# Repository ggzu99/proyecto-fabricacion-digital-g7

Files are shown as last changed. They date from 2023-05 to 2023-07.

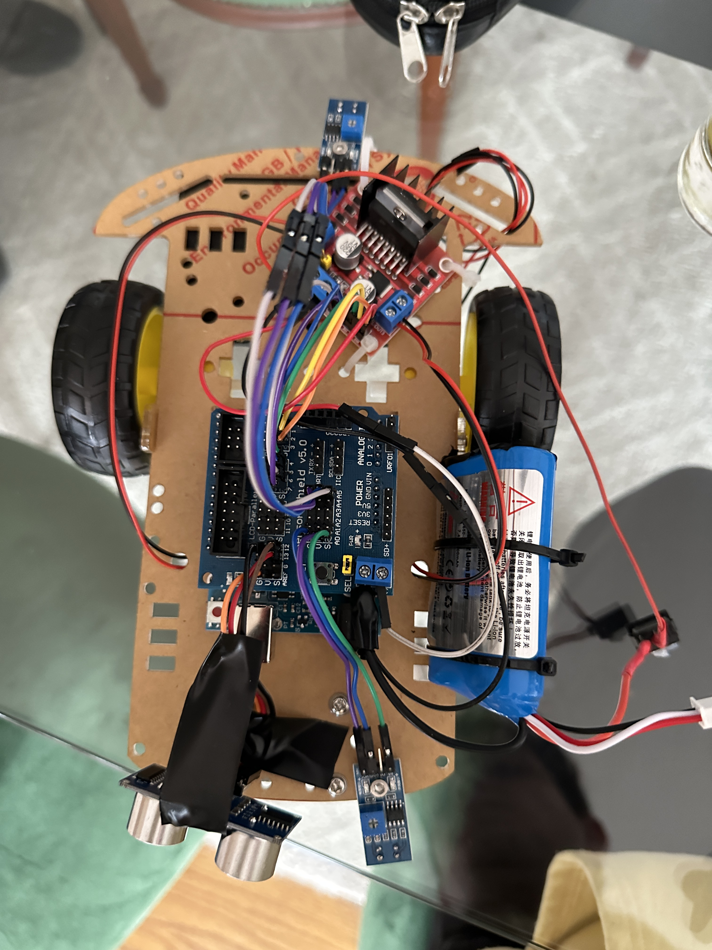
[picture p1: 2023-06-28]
Semana de Receso/MONTAJE_DE_PRUEBA_1.JPG

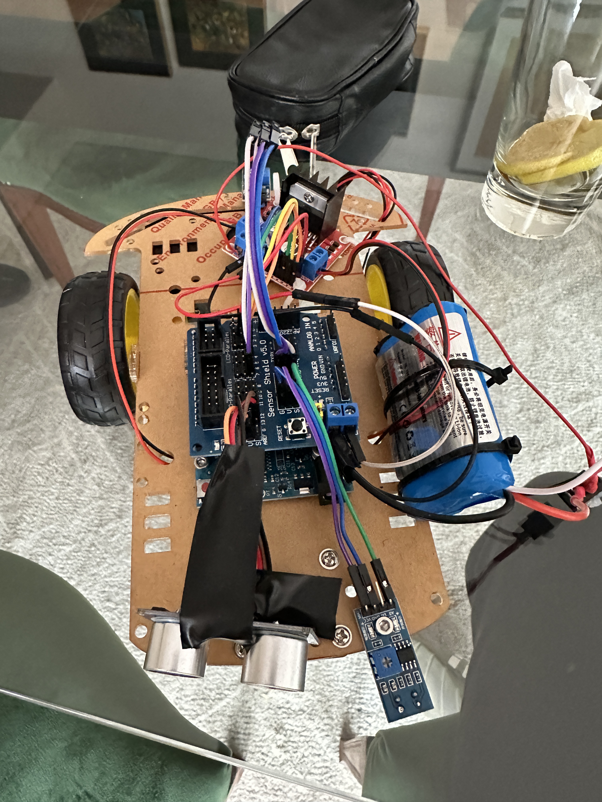
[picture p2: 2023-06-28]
Semana de Receso/MONTAJE_DE_PRUEBA_2.JPG

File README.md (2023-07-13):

# Proyecto "Robot Sumo" Grupo 7 + 6

En el presente repositorio se documentará el trabajo realizado para el proyecto semestral  
del ramo Fabricación Digital del departamento de ingeniería civil mecánica de la Universidad  
de Chile. 

Los avances semanales se encuentran ordenados por carpetas de nombre "Semana XX" donde XX corresponde a la  
semana de avance en cuestión. Los archivos actualizados y finales se encuentran en la carpeta "SEMANA 15". 

En la carpeta actualizada hay subcarpetas denominadas:
* **CAD**: Contiene todos los archivos CAD del proyecto, en formato universal .STP y un archivo PDF demostrativo de los componentes
  del robot.
* **MANUFACTURA**: Contiene el código g para manufacturar la parte inferior del chasis en Router CNC. Sumado a lo anterior tiene un
  documento llamado "Consideraciones Manufactura en CNC - Chasis Inferior" que entrega algunas consideraciones y recomendaciones
  para manufacturar el chasis.
* **STL**: Contiene los archivos .STL para poder procesar en software de impresión 3D e imprimir la cubierta de chasis, los soportes
  de sensores infrarojos, los soportes de motor y el portabatería.
* **SUMOCODE_FINAL**: Posee el archivo .ino correspondiente al código para cargar en el Arduino y que el robot funcione

Además, hay archivos adicionales, como "BOM FINAL" correspondiente a la lista de componentes y partes usadas y "Esquemático Sumobot",
el cual corresponde al esquemático electrónico del robot"

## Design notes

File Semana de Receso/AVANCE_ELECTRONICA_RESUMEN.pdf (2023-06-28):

1

Avances semana de receso - Electrónica

Para probar y hacer funcionar la electrónica de manera simple y rápida; con el fin de empezar a iterar el código y ojalá llegar a implementar una estrategia de batalla para el robot, se decidió comprar un kit robot de Arduino sigue líneas. Este incluía (en cuanto a electrónica):

- Arduino UNO
- Sensor Shield V5.0
- Controlador de Motores L298N
- 2 motores DC 3-6 V con reducción
- Sensor Ultrasónico HC-SR04

Sumado a los anteriores, se compraron dos (2) sensores infrarrojos TCRT-5000

Una vez adquiridos los componentes, se conectaron mediante el siguiente esquema, con algunas diferencias¹
:

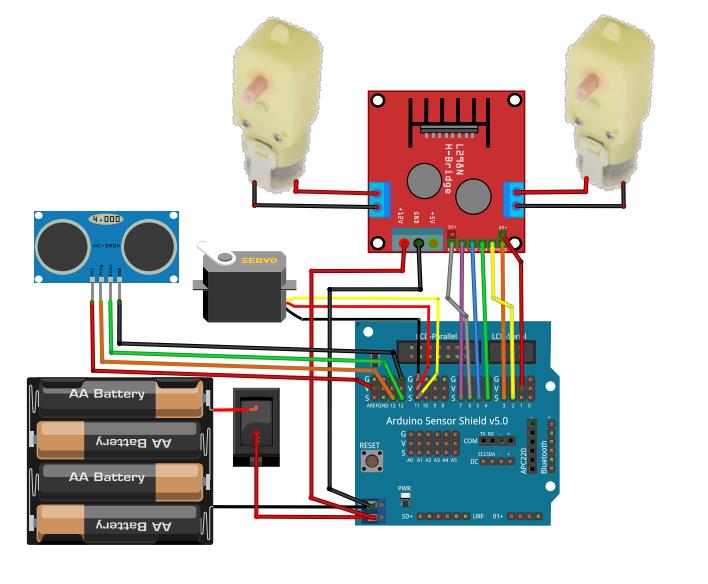
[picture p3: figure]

1
Se conectó la batería directamente al modulo controlador de motores L298N, de esa forma se aprovechó el regulador que trae, el cual al mantener el jumper activo (Fig 2.) permite tener una salida de 5V en VSS (Fig. 2), que sirve para suministrar corriente al Arduino y a la placa de sensores. Además no se utilizará el servomotor.

Figura 1. Esquemático.

2

Las conexiones realizadas fueron:

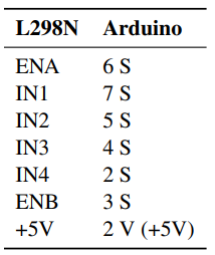
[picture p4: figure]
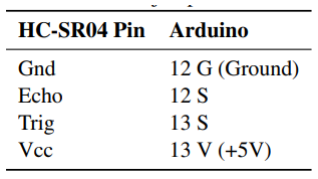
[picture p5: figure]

Como fuente de poder se está utilizando una batería LiPo de 7,4 V y 1800 mAh.

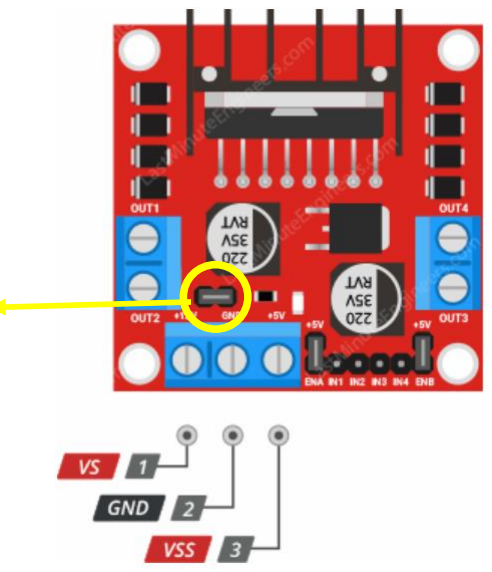
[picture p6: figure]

Figura 2. Power inputs and output L298N

JUMPER REGULADOR

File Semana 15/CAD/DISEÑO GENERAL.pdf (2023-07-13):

# Diseño General

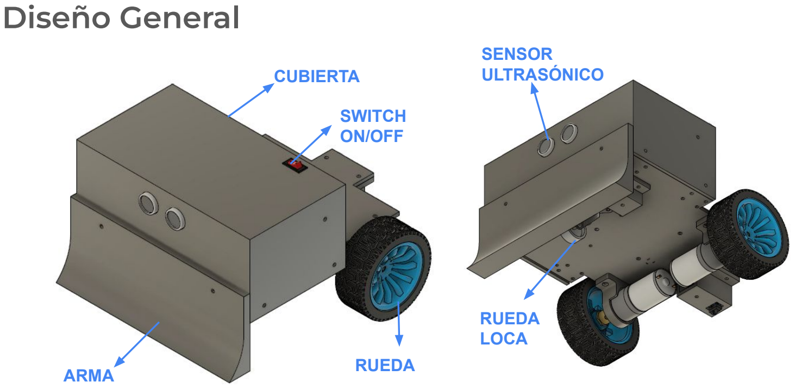
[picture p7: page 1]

ARMA

CUBIERTA

RUEDA

SWITCH
ON/OFF

SENSOR
ULTRASÓNICO

RUEDA
LOCA

# Diseño General

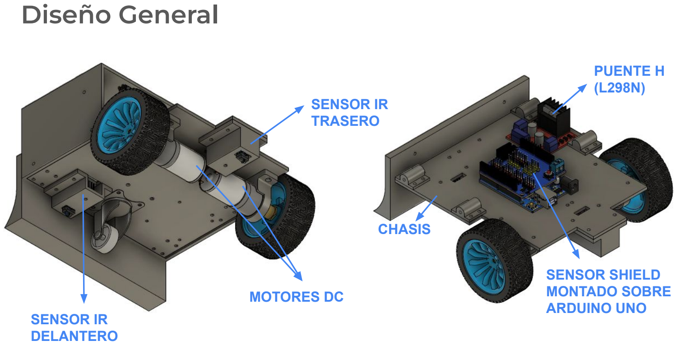
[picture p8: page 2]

MOTORES DC

SENSOR IR
TRASERO

SENSOR IR
DELANTERO

PUENTE H
(L298N)

SENSOR SHIELD
MONTADO SOBRE
ARDUINO UNO

CHASIS

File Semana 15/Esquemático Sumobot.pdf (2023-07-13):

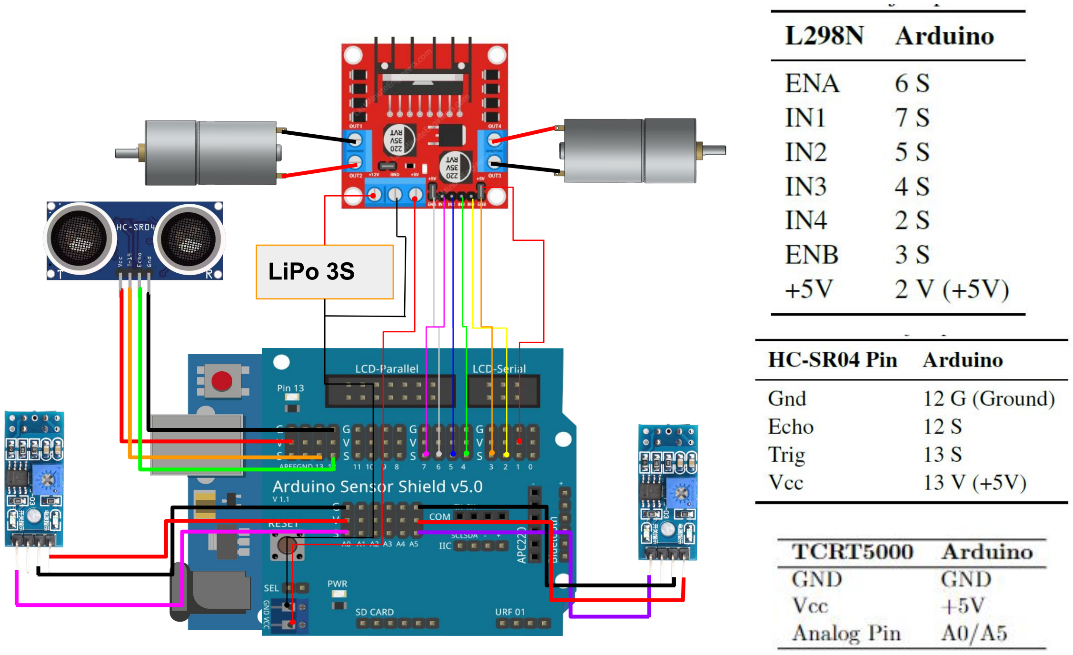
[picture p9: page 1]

LiPo 3S

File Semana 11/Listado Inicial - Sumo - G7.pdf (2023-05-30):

Curso: Fabricación Digital - ME4705-1 Diseño Conceptual

Listado inicial para desarrollo de Robot Sumo

1. Electrónica:
1.1. Arduino (ignacio)
1.2. Controlador de motores (ignacio)
1.3. Sensor Infrarrojo (Línea) (fablab)
1.4. Sensor Ultrasonico (Oponente) (fablab)
1.5. Motores (fablab)
1.6. Fuente de poder (fablab)
1.7. Switch encendido (fablab)
2. Mecánico:
2.1. Base (carton espuma - comprar)
2.2. Ruedas (fablab)
2.3. Arma (prototipo de carton)
3. Requerimientos de diseño:
3.1. 20 x 20 x 20 cm
3.2. <= 1000 g
3.3. No obstruir sensores del oponente

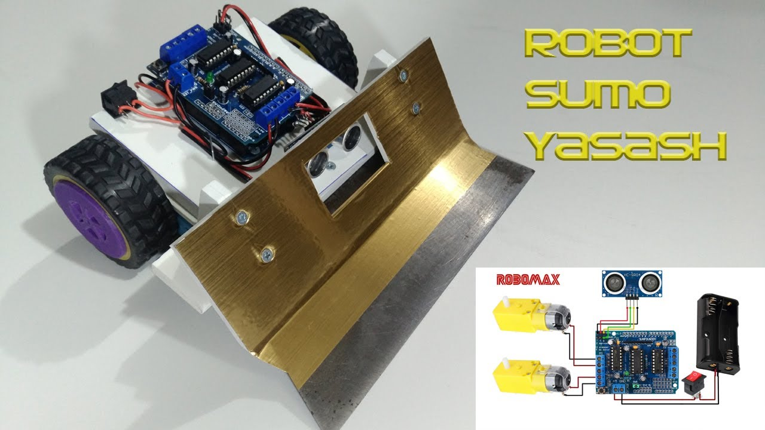
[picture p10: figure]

Links de interés:

- https://www.jsumo.com/sumo-robot-parts
- https://github.com/ggzu99/proyecto-fabricacion-digital-g7 ●

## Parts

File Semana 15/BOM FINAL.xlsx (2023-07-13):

BOM PARTES COMERCIALES SUMOBOT
Parte | Descripción | Cantidad | Tiendas (Chile)
Arduino UNO | Placa ARDUINO UNO R3 | 1 | AFEL (https://afel.cl/)
Sensor Shield | Placa para conectar sensores "Sensor Shield v5.0" que se monta sobre el Arduino | 1 | AFEL (https://afel.cl/)
LiPo 3S | Batería Lipo de 3 celdas, 11.1 V | 1 | REPUESTOSDRONE (https://repuestosdrone.cl/products/bateria-lipo-11-1v-1500-mah-35c-xt60?variant=35717458231447&currency=CLP)
Sensor Ultrasónico HC-SR04 | Sensor Ultrasónico para detectar enemigos | 1 | AFEL (https://afel.cl/)
Controlador de motor L298N | Controlador de motores que facilita la conexión a los mismos | 1 | AFEL (https://afel.cl/)
Sensor Infrarojo TCRT5000 | Sensor infrarojo para detectar línea blanca | 2 | AFEL (https://afel.cl/)
Ruedas 65 mm | Rueda traseras del robot de 65 mm de diámetro | 2 | RAMBAL (https://rambal.com/)
Rueda loca | Rueda delantera "Loca" | 1 | AFEL (https://afel.cl/)
Motor DC 12V | Motor DC 12V Modelo JGA25 100 RPM | 2 | RAMBAL (https://rambal.com/)
Acoplamiento Ruedas | Acoplamiento para ruedas Hexagonal 30x4 mm | 2 | RAMBAL (https://rambal.com/)
PERNERÍA
Tipo de Perno | Dimensiones | Cantidad | Tienda
ALLEN/PARKER | M3x10 mm | 32 | PERNOS KIM
ALLEN/PARKER | M3x8 mm | 4 | PERNOS KIM
ALLEN/PARKER | M3x20mm | 10 | PERNOS KIM

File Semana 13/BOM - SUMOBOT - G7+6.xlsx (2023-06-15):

Nombre de componente | Qty | Unit Cost | Total
Kit Arduino DIY Robot: | 1 | $36990 | $36990
Arduino UNO R3 | 1
Cable USB | 1
Shield expansión V5.0
Controlador de motor L298N | 1
Sensor Ultrasónico HC-SR04 | 1
Servomotor SG90 | 1
Placa fija de servomotor | 1
Motor DC | 2
Ruedas | 2
Rueda Libre | 1
Encoder 20 PPR | 2
Portapilas 4 x AA | 1
Placa acrílica chasis | 1
Sensor infrarojo TCRT5000 | 2 | $2300 | $4600
TOTAL |  |  | $41590

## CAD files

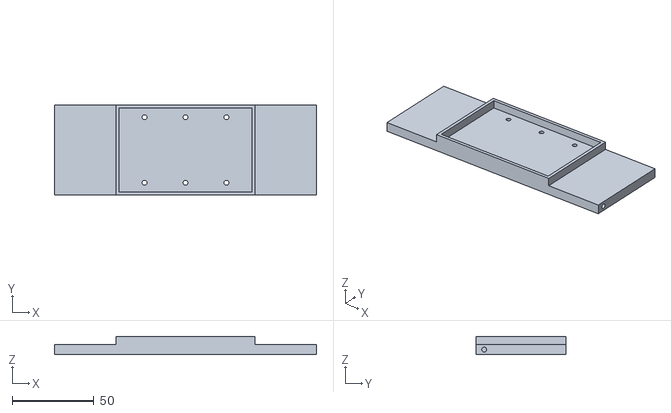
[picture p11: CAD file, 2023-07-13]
Semana 15/STL/portabatería.stl
160.0 x 55.0 x 11.0

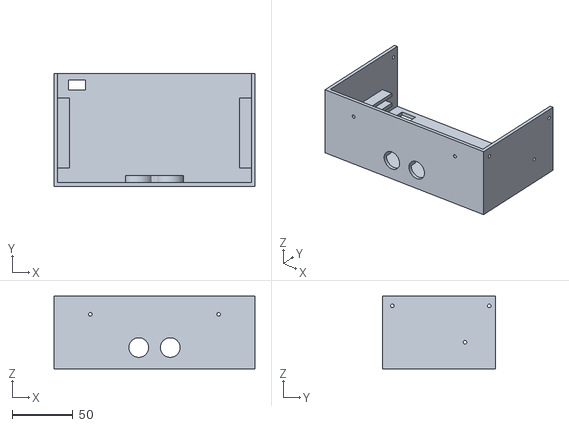
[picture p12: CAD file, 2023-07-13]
Semana 15/STL/cubierta.stl
166.0 x 93.0 x 60.0

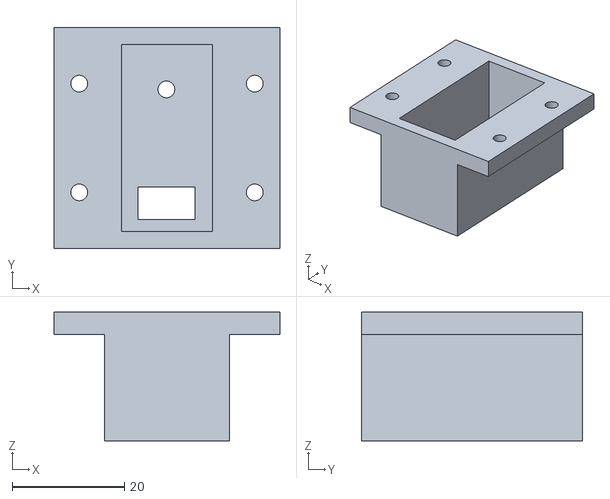
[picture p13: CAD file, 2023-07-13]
Semana 15/STL/soporte_IR_Trasero.stl
40.3 x 39.4 x 23.0

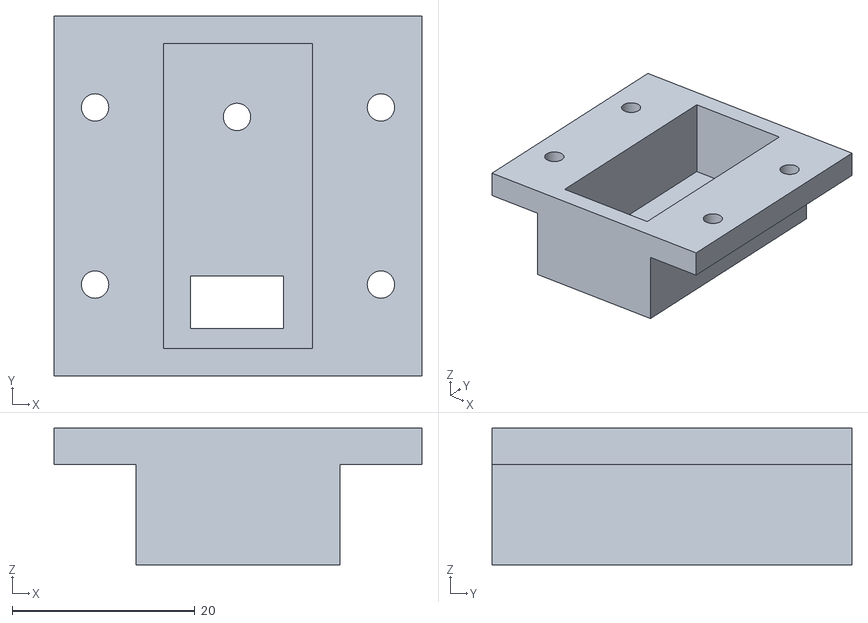
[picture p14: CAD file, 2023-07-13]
Semana 15/STL/soporte_IR_delantero.stl
40.3 x 39.4 x 15.0

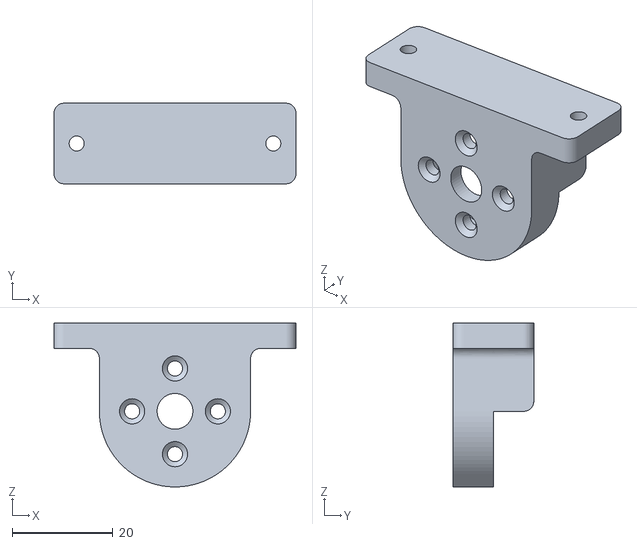
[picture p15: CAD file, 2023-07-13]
Semana 15/STL/motor_mount.stl
48.0 x 16.0 x 32.5

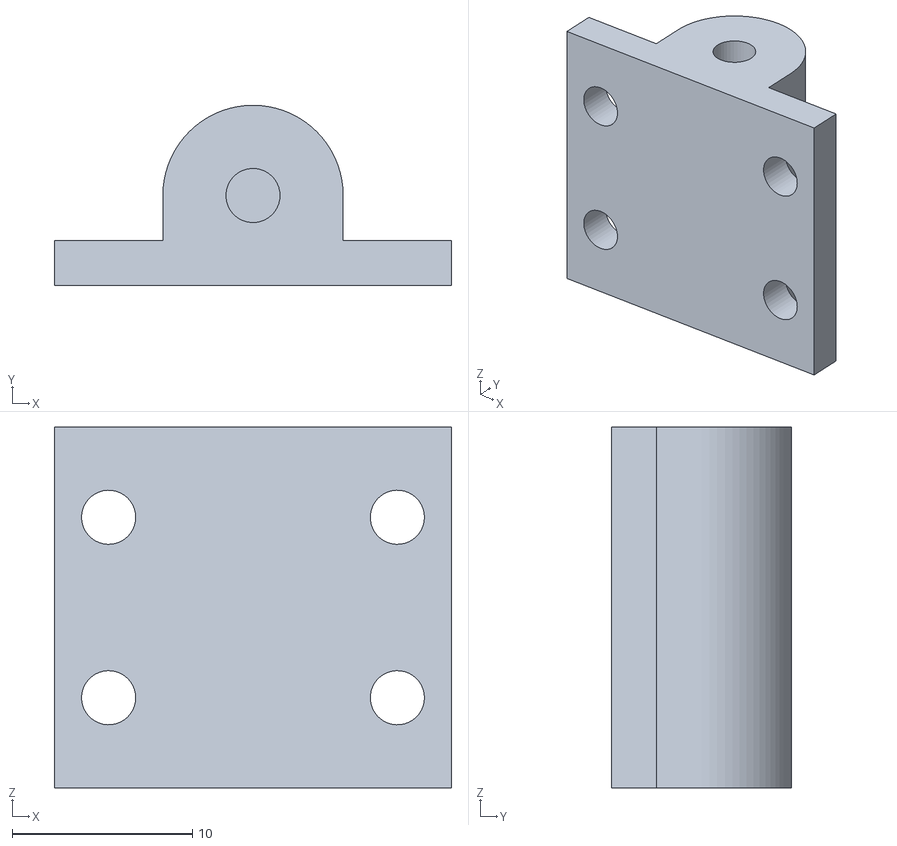
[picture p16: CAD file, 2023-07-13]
Semana 15/STL/fijaciones chasis-cubierta.stl
22.0 x 10.0 x 20.0

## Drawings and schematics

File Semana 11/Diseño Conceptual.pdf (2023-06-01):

# Sheman -

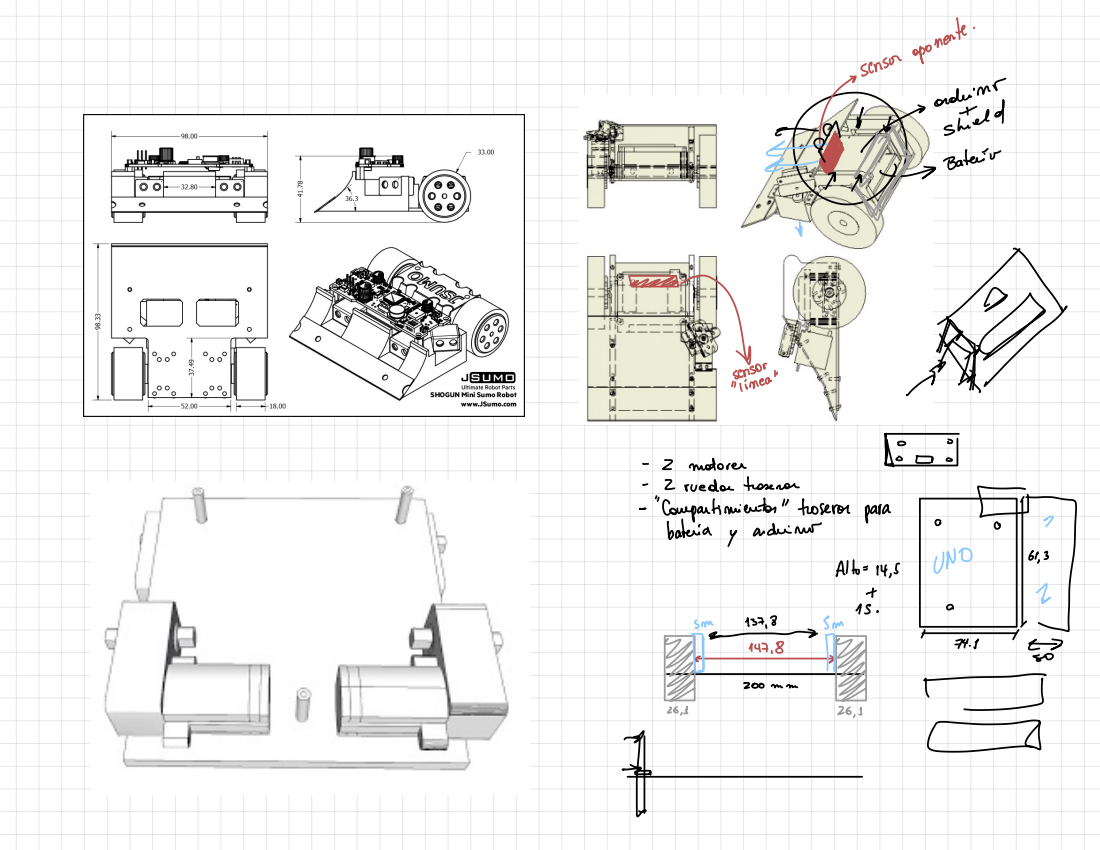
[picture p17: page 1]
sor; "limea"; motoren; rueden; tran; "Compartimiento"troseros; para; bateria; adeinu; Alto=14,; UNO

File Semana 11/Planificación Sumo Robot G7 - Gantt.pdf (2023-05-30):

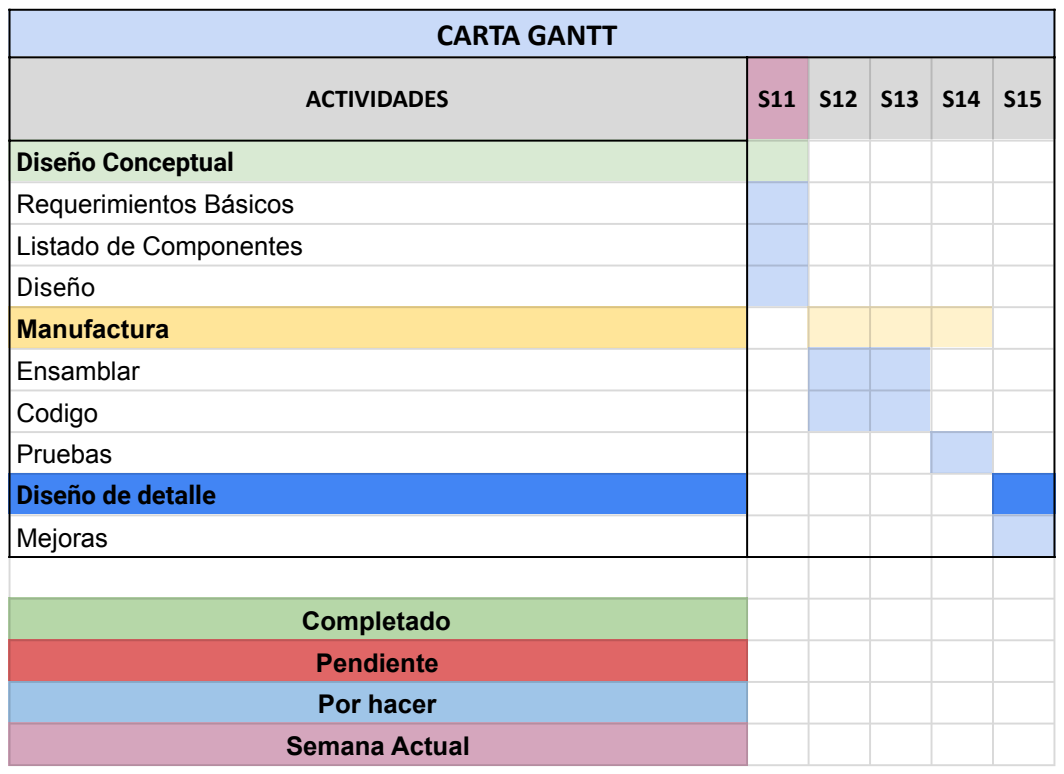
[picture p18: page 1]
CARTA GANTT

ACTIVIDADES | S11 | S12 S13 S14 S15

Diseño Conceptual
Requerimientos Básicos Listado de Componentes Diseño

Manufactura
Ensamblar Codigo Pruebas

Diseño de detalle
Mejoras

Completado
Pendiente
Por hacer
Semana Actual

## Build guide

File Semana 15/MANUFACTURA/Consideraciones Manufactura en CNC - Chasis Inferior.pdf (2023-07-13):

Consideraciones e Indicaciones Manufactura en Router CNC – Chasis – Parte Inferior

El presente documento tiene como intención guiar en la manufactura de posibles réplicas a realizar de nuestro robot Sumo. En específico se detallan las consideraciones tomadas, las herramientas utilizadas y se explica de forma general el proceso de manufactura realizado.

El código g para replicar esta parte se denomina “Chasis_INFERIOR_gcode” y se encuentra en el repositorio.

Para manufacturarlo se utilizó:

- Acrílico de 3mm de espesor y dimensiones 250 x 250 mm
- Una fresa de una sola flauta “O-Flute” de 1,5 mm de diámetro (este tipo de fresa permite la mejor disipación de calor y la mejor terminación cuando se trabaja con acrílicos o plásticos, ya que no derrite el material), Cuyas características principales se observan en la siguiente imagen y se puede adquirir en Aliexpress, (https://es.aliexpress.com/item/32966808264.html) escogiendo el modelo SP1F-D1.5-L05.

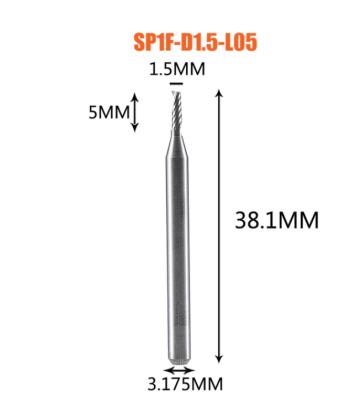
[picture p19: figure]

- Como parámetros de corte (según lo recomendado por el fabricante, ver imagen siguiente):
- Spindle Speed: 17.000 RPM
- Feed Speed: 2000 mm/min

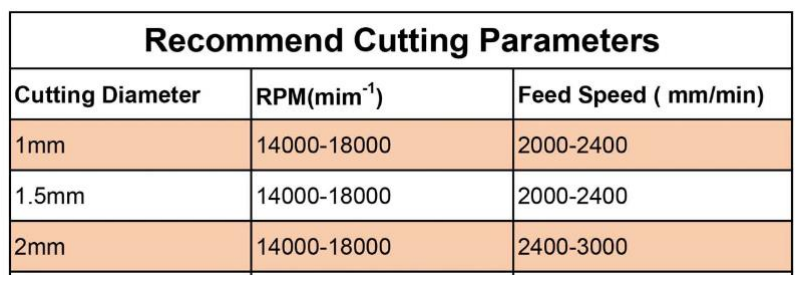
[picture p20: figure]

- Como stock, se configuró un “Fixed Size Box” de 180 x 160 x 3 mm

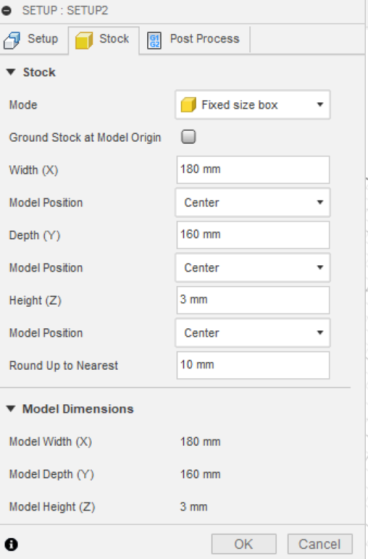
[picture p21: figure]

Consideraciones e Indicaciones Manufactura en Router CNC – Chasis – Parte Inferior

- Operación de Contorno 2D
- Múltiples pasadas de corte, con un máximo por bajada de 1 mm
- Se chequeo la opción de permitir tabs a la hora de cortar el contorno, para que el material no se moviera previo a finalizar todos los orificios
- Las imágenes y videos del proceso de manufactura se encuentran en el repositorio.

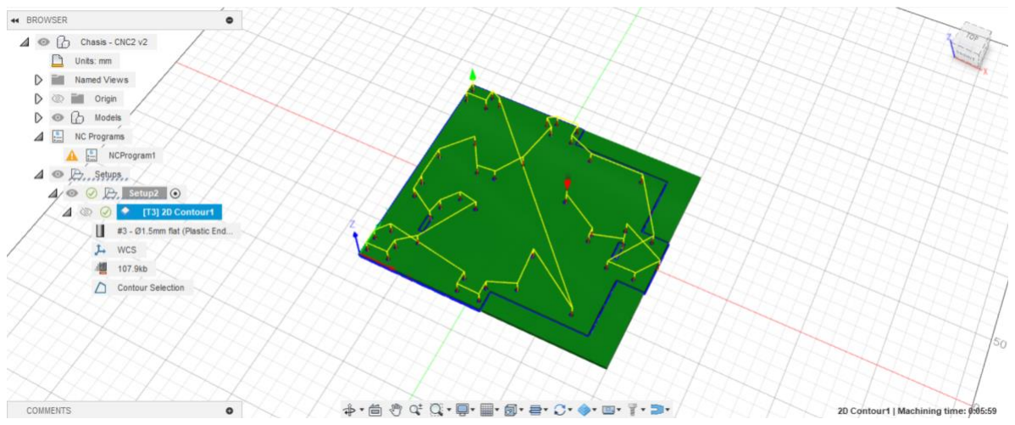
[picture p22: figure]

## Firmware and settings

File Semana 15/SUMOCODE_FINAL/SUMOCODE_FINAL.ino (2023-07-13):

#include <Ultrasonic.h> //Librería que facilita el uso de sensores ultrasonicos, con ella no es necesario definir los trig and
//echo pin, sino que se usa la notacion Ultrasonic ultrasonic()

//LINK LIBRERIA: https://github.com/ErickSimoes/Ultrasonic/tree/master

//DEFINICION DE PINES--------------------------------------------------------------------------------------
Ultrasonic ultrasonic(13,12);

//Pines asociados a motores
const int IN1=7;
const int IN2=5;
const int IN3=4;
const int IN4=2;
const int enAPin = 6; // Pin para control PWM del motor DC IZQUIERDO
const int enBPin = 3; // Pin para control PWM del motor DC DERECHO

//Pines analógicos asociados a Sensores IR
#define IR_sensor_front A0 // Sensor IR delantero
#define IR_sensor_back A5 // Sensor IR trasero
int distance ;
//----------------------------------------------------------------------------------------------------------





void setup() 
{
Serial.begin(9600);
delay (5000); // Esperamos 5 segundos antes de partir
}




void loop()
{
 int IR_front = analogRead(IR_sensor_front); //Leemos sensor delantero
 int IR_back = analogRead(IR_sensor_back);   //Leemos sensor trasero
 distance = ultrasonic.read();  //Leemos distancia ultrasonico


 
     if(IR_front < 50) {
        BACKWARD(255);

     } else if (IR_back < 50) {
        FORWARD(255);

     } else if (distance <= 60) {
        FORWARD(255);

     } else {
       search();
            
     }

//Debugging
  Serial.print("Distance in CM: ");
  Serial.println(distance);
  Serial.println("IR front :");
  Serial.println(IR_front); 
  Serial.println("IR back :");
  Serial.println(IR_back);  
 

} 



//FUNCIONES PARA CONTROL DE MOTORES//------
void FORWARD (int Speed){
  //FUNCION AVANZAR
  analogWrite(enAPin, Speed);  // Set motor A speed
  analogWrite(enBPin, Speed);  // Set motor B speed
  digitalWrite(IN1,HIGH);
  digitalWrite(IN2,LOW);
  digitalWrite(IN3,HIGH);
  digitalWrite(IN4,LOW);
}//--------------------------------------------
void BACKWARD (int Speed){
  //FUNCION DE RETROCESO
  analogWrite(enAPin, Speed);  // Set motor A speed
  analogWrite(enBPin, Speed);  // Set motor B speed
  digitalWrite(IN1,LOW);
  digitalWrite(IN2,HIGH);
  digitalWrite(IN3,LOW);
  digitalWrite(IN4,HIGH);
}//--------------------------------------------
void ROTATE (int Speed)
{
  //FUNCION DE ROTACION 
  analogWrite(enAPin, Speed);  // Set motor A speed
  analogWrite(enBPin, Speed);  // Set motor B speed
  digitalWrite(IN1,HIGH);
  digitalWrite(IN2,LOW);
  digitalWrite(IN3,LOW);
  digitalWrite(IN4,HIGH);
}//--------------------------------------------
void Stop(){
  //FUNCION DE PARADA DE MOTORES
  analogWrite(enAPin, 0);  // Set motor A speed
  analogWrite(enBPin, 0);  // Set motor B speed
  digitalWrite(IN1,LOW);
  digitalWrite(IN2,LOW);
  digitalWrite(IN3,LOW);
  digitalWrite(IN4,LOW);
}
//FUNCION DE BUSQUEDA, ROTAR(100)
void search(){
  ROTATE(100);



}

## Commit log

2023-05-30 Create README.md
    Creacion de readme para descripcion del proyecto a realizar
2023-05-30 Semana 11
    Avances Semana 11:
    * carta gantt
    * levantamiento de requerimientos basicos
2023-06-01 Diseño Conceptual
    Dibujos y referencias para diseño conceptual - 01/06
2023-06-15 Semana 13
    Avances Semana 13
    [BOM - SUMOBOT - G7+6.xlsx]
2023-06-15 Bill of Materials
    Update 15/06 16:46 hr
    [BOM - SUMOBOT - G7+6.xlsx]
2023-06-15 Delete BOM - SUMOBOT - G7+6.xlsx
    Actualizacion
    [BOM - SUMOBOT - G7+6.xlsx]
2023-06-15 Semana 13 Carpeta actualizada
    [BOM - SUMOBOT - G7+6.xlsx]
2023-06-15 Carpeta Semana 13
    Semana 13 Update
    [BOM - SUMOBOT - G7+6.xlsx, Kanban_S13_G6+7_SUMOBOT.xlsx]
2023-06-28 Avances Semana de Receso
    Se incluye primera iteracion del codigo, explicativo conexiones electrónica e imagenes del montaje de prueba.
2023-07-13 Ultima Actualización de archivos
    [BOM FINAL.xlsx, cubierta.stl, fijaciones chasis-cubierta.stl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]
